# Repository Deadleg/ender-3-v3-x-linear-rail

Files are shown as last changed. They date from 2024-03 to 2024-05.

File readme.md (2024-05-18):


# Ender-3-v3-se-x-linear-rail
This mod replaces the X-axis v slot wheels with an MGN9 linear rail.

If you don't know if you need linear rails on the X-axis then you probably won't benefit from this. But if you
_want_ linear rails like I did, then enjoy.

- **Dimensional accuracy and flow calibration is required in order for the nut trap to fit the nuts securely**.
- [BOM](bom/bom.csv).
  - Either an MGN9C or MGN9H carriage can be used. Ideally use rails with some preload to improve wobble along the Y
  axis.
- Use [Voron print settings](https://docs.vorondesign.com/sourcing.html#print-settings).
  - Probably avoid PLA due to the nut trap only being two walls thick.
- No additional supports required.
- Print STLs in their default orientation.

After installation remember to re-calibrate the Z-offset and recreate the bed mesh.

Measurements and spacers inspired by https://www.printables.com/model/716958-linear-x-rail-mod-ender-3-v3-se. This
version doesn't sacrifice X-axis movement and doesn't need a new endstop. The nozzle sits a bit forward in the Y
axis.

See [results.md](results.md) for input shaper results.

Ender 3 V3 SE reference model taken from
https://www.printables.com/model/672045-ender-3-v3-se-reference-models-step-files.

# Development

Prerequisites:

- https://github.com/nophead/NopSCADlib/tree/master
- https://github.com/revarbat/BOSL

PYTHONPATH is required to generate the BOM with costs:

```bash
PYTHONPATH=$PWD ~/.local/share/OpenSCAD/libraries/NopSCADlib/scripts/make_all.py
```

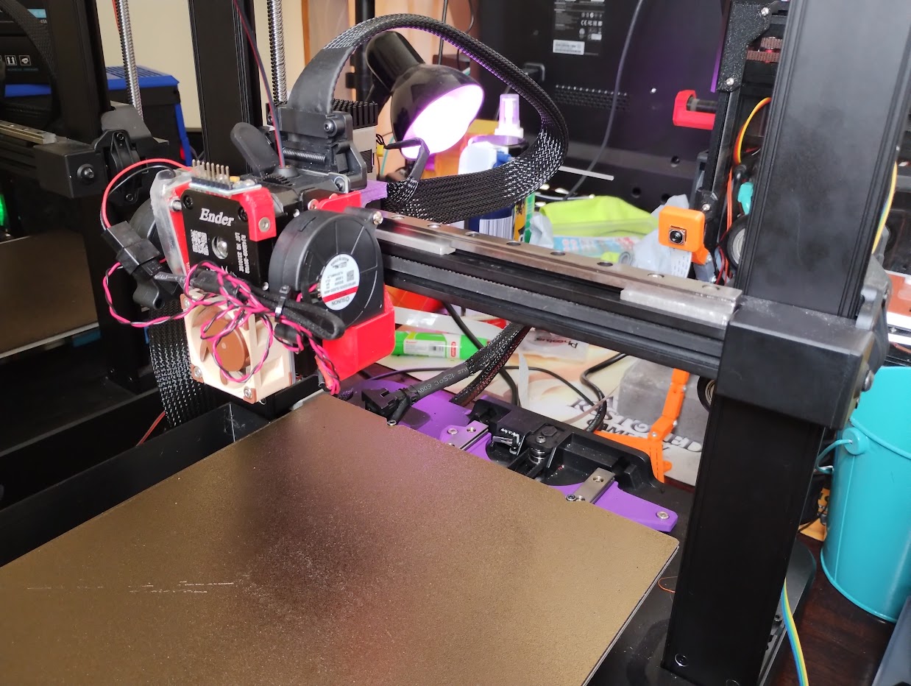
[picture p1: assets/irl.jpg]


<span></span>

---
## Table of Contents
1. [Parts list](#Parts_list)
1. [Carriage Assembly](#carriage_assembly)
1. [Linear Rail Assembly](#linear_rail_assembly)
1. [Carriage Rail Assembly](#carriage_rail_assembly)
1. [Toolhead Carriage Assembly](#toolhead_carriage_assembly)

<span></span>
[Top](#TOP)

---

## Parts list
| <span style="writing-mode: vertical-rl; text-orientation: mixed;">Carriage</span> | <span style="writing-mode: vertical-rl; text-orientation: mixed;">Linear&nbsp;Rail</span> | <span style="writing-mode: vertical-rl; text-orientation: mixed;">Carriage&nbsp;Rail</span> | <span style="writing-mode: vertical-rl; text-orientation: mixed;">Toolhead&nbsp;Carriage</span> | <span style="writing-mode: vertical-rl; text-orientation: mixed;">TOTALS</span> |  |
|---:|---:|---:|---:|---:|:---|
|  |  |  |  | | **Vitamins** |
| &nbsp;&nbsp;.&nbsp; | &nbsp;&nbsp;7&nbsp; | &nbsp;&nbsp;.&nbsp; | &nbsp;&nbsp;.&nbsp; |  &nbsp;&nbsp;7&nbsp; | &nbsp;&nbsp; Linear rail MGN9 x 300mm |
| &nbsp;&nbsp;.&nbsp; | &nbsp;&nbsp;1&nbsp; | &nbsp;&nbsp;.&nbsp; | &nbsp;&nbsp;.&nbsp; |  &nbsp;&nbsp;1&nbsp; | &nbsp;&nbsp; Linear rail carriage MGN9C |
| &nbsp;&nbsp;.&nbsp; | &nbsp;&nbsp;7&nbsp; | &nbsp;&nbsp;.&nbsp; | &nbsp;&nbsp;.&nbsp; |  &nbsp;&nbsp;7&nbsp; | &nbsp;&nbsp; Nut M3 hammer |
| &nbsp;&nbsp;2&nbsp; | &nbsp;&nbsp;.&nbsp; | &nbsp;&nbsp;.&nbsp; | &nbsp;&nbsp;.&nbsp; |  &nbsp;&nbsp;2&nbsp; | &nbsp;&nbsp; Nut M5 x 4mm  |
| &nbsp;&nbsp;.&nbsp; | &nbsp;&nbsp;.&nbsp; | &nbsp;&nbsp;4&nbsp; | &nbsp;&nbsp;.&nbsp; |  &nbsp;&nbsp;4&nbsp; | &nbsp;&nbsp; Screw M3 cap x  8mm |
| &nbsp;&nbsp;.&nbsp; | &nbsp;&nbsp;7&nbsp; | &nbsp;&nbsp;.&nbsp; | &nbsp;&nbsp;.&nbsp; |  &nbsp;&nbsp;7&nbsp; | &nbsp;&nbsp; Screw M3 cap x 10mm |
| &nbsp;&nbsp;.&nbsp; | &nbsp;&nbsp;.&nbsp; | &nbsp;&nbsp;.&nbsp; | &nbsp;&nbsp;2&nbsp; |  &nbsp;&nbsp;2&nbsp; | &nbsp;&nbsp; Screw M5 wafer head x  4mm |
| &nbsp;&nbsp;.&nbsp; | &nbsp;&nbsp;.&nbsp; | &nbsp;&nbsp;4&nbsp; | &nbsp;&nbsp;.&nbsp; |  &nbsp;&nbsp;4&nbsp; | &nbsp;&nbsp; Washer  M3 x 7mm x 0.5mm |
| &nbsp;&nbsp;2&nbsp; | &nbsp;&nbsp;22&nbsp; | &nbsp;&nbsp;8&nbsp; | &nbsp;&nbsp;2&nbsp; | &nbsp;&nbsp;34&nbsp; | &nbsp;&nbsp;Total vitamins count |
|  |  |  |  | | **3D printed parts** |
| &nbsp;&nbsp;.&nbsp; | &nbsp;&nbsp;1&nbsp; | &nbsp;&nbsp;.&nbsp; | &nbsp;&nbsp;.&nbsp; |  &nbsp;&nbsp;1&nbsp; | &nbsp;&nbsp;left_spacer.stl |
| &nbsp;&nbsp;.&nbsp; | &nbsp;&nbsp;1&nbsp; | &nbsp;&nbsp;.&nbsp; | &nbsp;&nbsp;.&nbsp; |  &nbsp;&nbsp;1&nbsp; | &nbsp;&nbsp;middle_spacer.stl |
| &nbsp;&nbsp;.&nbsp; | &nbsp;&nbsp;1&nbsp; | &nbsp;&nbsp;.&nbsp; | &nbsp;&nbsp;.&nbsp; |  &nbsp;&nbsp;1&nbsp; | &nbsp;&nbsp;right_spacer.stl |
| &nbsp;&nbsp;1&nbsp; | &nbsp;&nbsp;.&nbsp; | &nbsp;&nbsp;.&nbsp; | &nbsp;&nbsp;.&nbsp; |  &nbsp;&nbsp;1&nbsp; | &nbsp;&nbsp;toolhead_carriage_MGN9C.stl |
| &nbsp;&nbsp;1&nbsp; | &nbsp;&nbsp;.&nbsp; | &nbsp;&nbsp;.&nbsp; | &nbsp;&nbsp;.&nbsp; |  &nbsp;&nbsp;1&nbsp; | &nbsp;&nbsp;toolhead_carriage_MGN9H.stl |
| &nbsp;&nbsp;2&nbsp; | &nbsp;&nbsp;3&nbsp; | &nbsp;&nbsp;.&nbsp; | &nbsp;&nbsp;.&nbsp; | &nbsp;&nbsp;5&nbsp; | &nbsp;&nbsp;Total 3D printed parts count |

<span></span>
[Top](#TOP)

---

## Carriage Assembly
### Vitamins
|Qty|Description|
|---:|:---|
|2| Nut M5 x 4mm |

### 3D Printed parts

| 1 x toolhead_carriage_MGN9C.stl | 1 x toolhead_carriage_MGN9H.stl |
|---|---|
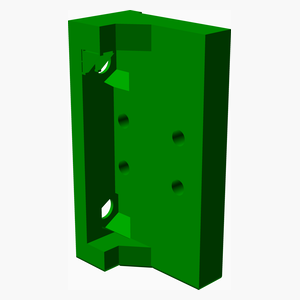
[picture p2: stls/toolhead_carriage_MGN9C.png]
toolhead_carriage_MGN9C.stl
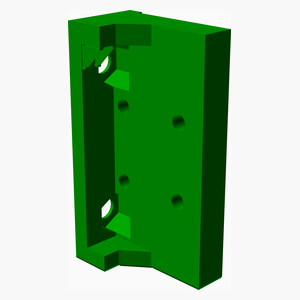
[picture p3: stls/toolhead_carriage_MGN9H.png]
toolhead_carriage_MGN9H.stl
|  |  

### Assembly instructions
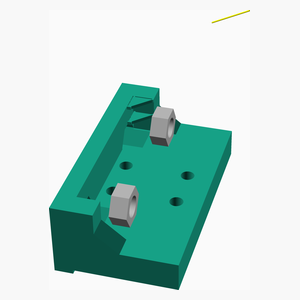
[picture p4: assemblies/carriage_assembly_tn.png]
carriage_assembly


First remove the two supports at the top of the model.

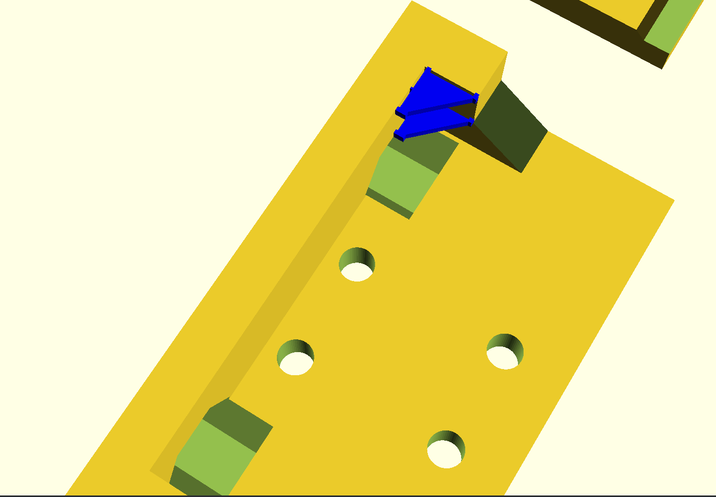
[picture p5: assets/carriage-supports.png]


The nuts should be a tight fit. If you have trouble pushing the nut in, check if there is any substantial corner
blobbing due to lack of pressure advance and/or insert an M5 screw from the otherside and tighten.

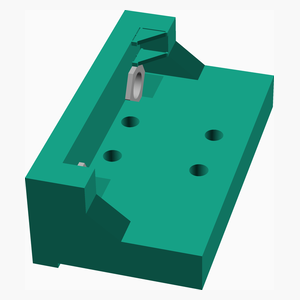
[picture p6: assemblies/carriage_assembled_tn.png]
carriage_assembled


<span></span>
[Top](#TOP)

---

## Linear Rail Assembly
### Vitamins
|Qty|Description|
|---:|:---|
|7| Linear rail MGN9 x 300mm|
|1| Linear rail carriage MGN9C|
|7| Nut M3 hammer|
|7| Screw M3 cap x 10mm|

### 3D Printed parts

| 1 x left_spacer.stl | 1 x middle_spacer.stl | 1 x right_spacer.stl |
|---|---|---|
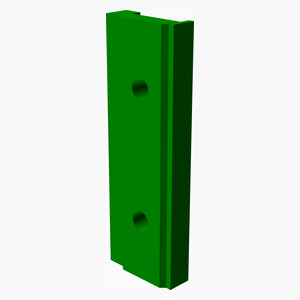
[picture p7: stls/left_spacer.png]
left_spacer.stl
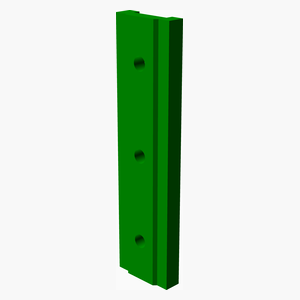
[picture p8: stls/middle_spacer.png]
middle_spacer.stl
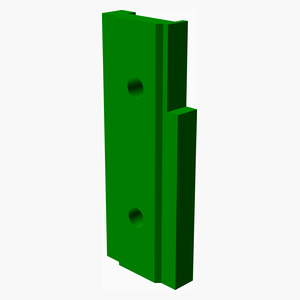
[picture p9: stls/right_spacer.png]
right_spacer.stl
|  |  |  

### Assembly instructions
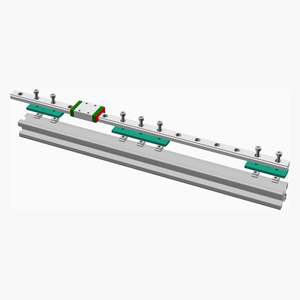
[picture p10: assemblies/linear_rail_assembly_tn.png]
linear_rail_assembly


Attach the spacers to the assembly, taking note that the left spacer is offset by one screw hole.

Remember to clean and lubricate both the carriage and rail.

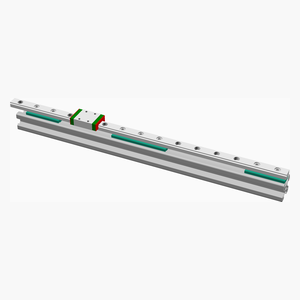
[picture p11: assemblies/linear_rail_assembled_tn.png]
linear_rail_assembled


<span></span>
[Top](#TOP)

---

## Carriage Rail Assembly
### Vitamins
|Qty|Description|
|---:|:---|
|4| Screw M3 cap x  8mm|
|4| Washer  M3 x 7mm x 0.5mm|

### Sub-assemblies

| 1 x carriage_assembly | 1 x linear_rail_assembly |
|---|---|
| carriage_assembled | linear_rail_assembled 

### Assembly instructions
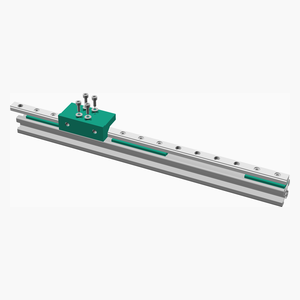
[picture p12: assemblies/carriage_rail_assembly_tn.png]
carriage_rail_assembly


Attach the carriage to the rail. Note that the front two screws won't be easily accessible once the PCB is mounted.

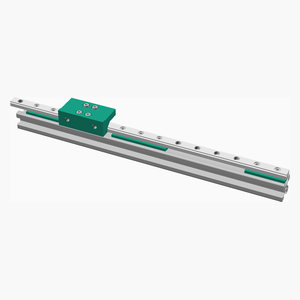
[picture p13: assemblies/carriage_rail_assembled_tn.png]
carriage_rail_assembled


<span></span>
[Top](#TOP)

---

## Toolhead Carriage Assembly
### Vitamins
|Qty|Description|
|---:|:---|
|2| Screw M5 wafer head x  4mm|

### Sub-assemblies

| 1 x carriage_rail_assembly |
|---|
| carriage_rail_assembled 

### Assembly instructions
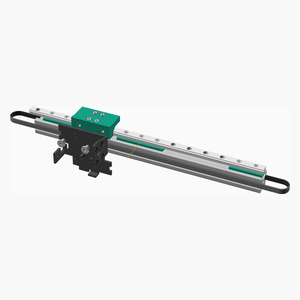
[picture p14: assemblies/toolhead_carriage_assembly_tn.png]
toolhead_carriage_assembly


Screw the frame into the carriage, ensuring that the frame is flush on the carriage. Remember to insert the belts
before re-assembling the everything else.

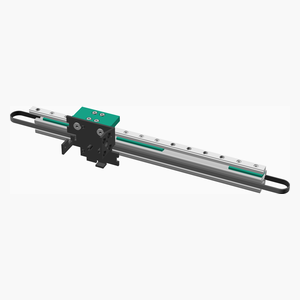
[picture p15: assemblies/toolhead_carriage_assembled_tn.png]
toolhead_carriage_assembled


<span></span>
[Top](#TOP)

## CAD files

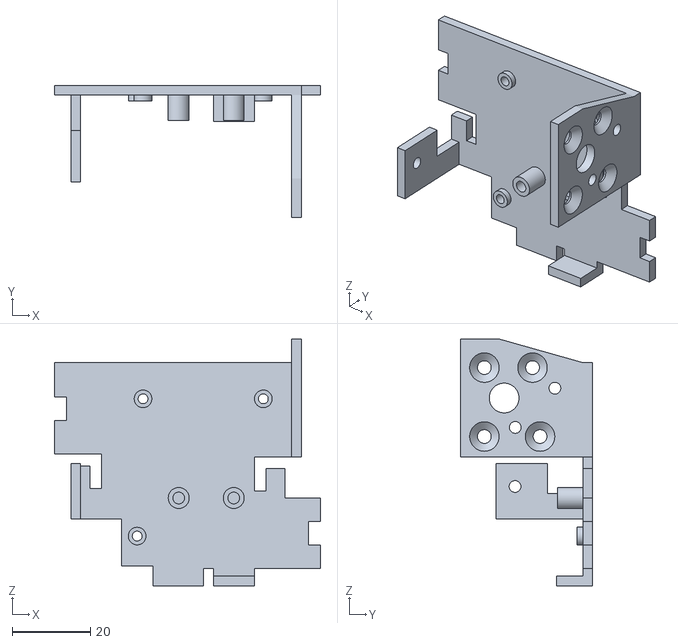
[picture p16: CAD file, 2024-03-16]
ender-3-v3-se-reference-models-step-files/frame.stl
67.8 x 33.7 x 62.9

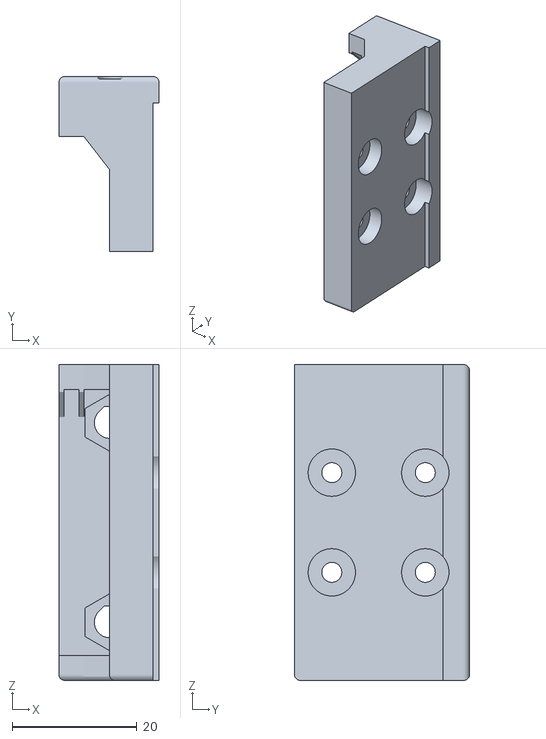
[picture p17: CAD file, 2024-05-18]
stls/toolhead_carriage_MGN9H.stl
16.1 x 28.1 x 50.7

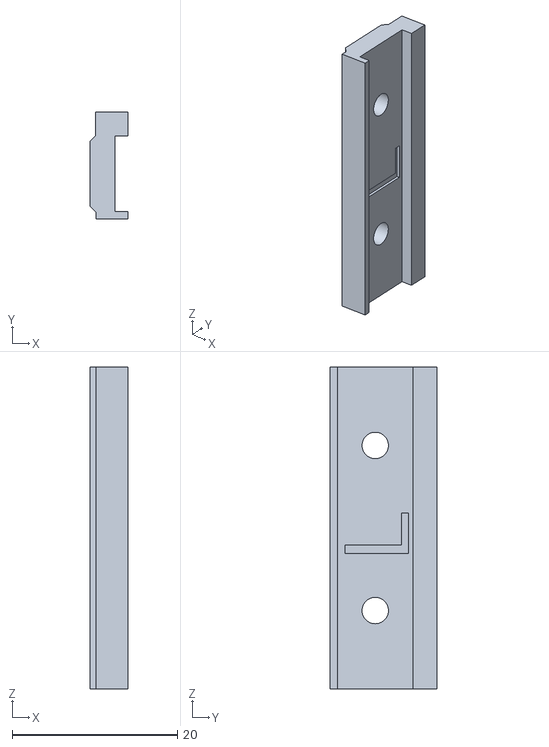
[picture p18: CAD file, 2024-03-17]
stls/left_spacer.stl
4.60 x 13.0 x 39.0

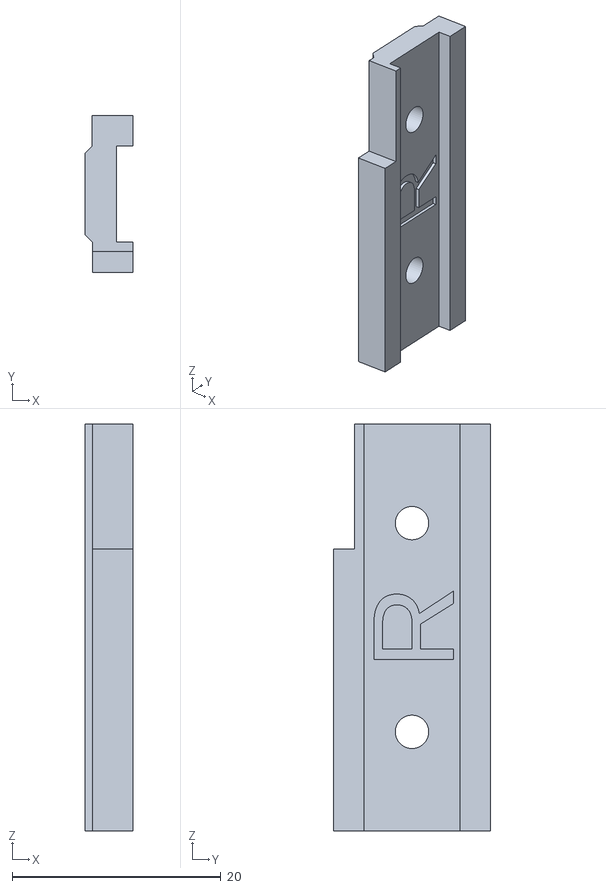
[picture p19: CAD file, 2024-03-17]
stls/right_spacer.stl
4.60 x 15.0 x 39.0

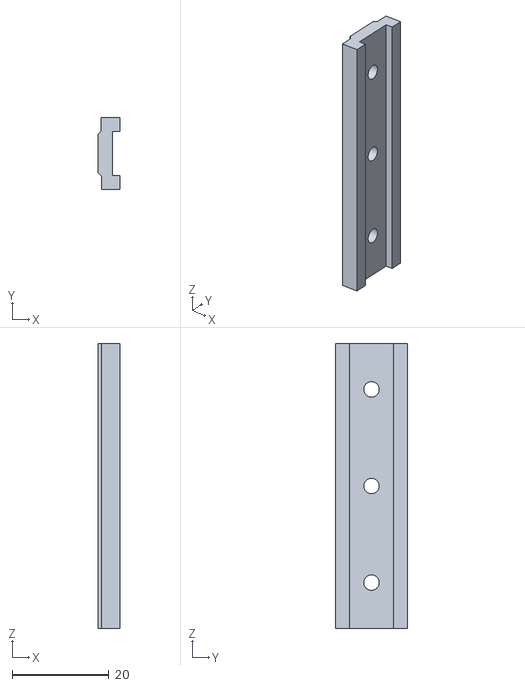
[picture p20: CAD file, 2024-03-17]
stls/middle_spacer.stl
4.60 x 15.0 x 59.0

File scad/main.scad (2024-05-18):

//! This mod replaces the X-axis v slot wheels with an MGN9 linear rail.
//!
//! If you don't know if you need linear rails on the X-axis then you probably won't benefit from this. But if you
//! _want_ linear rails like I did, then enjoy.
//!
//! - **Dimensional accuracy and flow calibration is required in order for the nut trap to fit the nuts securely**.
//! - [BOM](bom/bom.csv).
//!   - Either an MGN9C or MGN9H carriage can be used. Ideally use rails with some preload to improve wobble along the Y
//!   axis.
//! - Use [Voron print settings](https://docs.vorondesign.com/sourcing.html#print-settings).
//!   - Probably avoid PLA due to the nut trap only being two walls thick.
//! - No additional supports required.
//! - Print STLs in their default orientation.
//!
//! After installation remember to re-calibrate the Z-offset and recreate the bed mesh.
//!
//! Measurements and spacers inspired by https://www.printables.com/model/716958-linear-x-rail-mod-ender-3-v3-se. This
//! version doesn't sacrifice X-axis movement and doesn't need a new endstop. The nozzle sits a bit forward in the Y
//! axis.
//!
//! See [results.md](results.md) for input shaper results.
//!
//! Ender 3 V3 SE reference model taken from
//! https://www.printables.com/model/672045-ender-3-v3-se-reference-models-step-files.
//!
//! # Development
//!
//! Prerequisites:
//!
//! - https://github.com/nophead/NopSCADlib/tree/master
//! - https://github.com/revarbat/BOSL
//!
//! PYTHONPATH is required to generate the BOM with costs:
//!
//! ```bash
//! PYTHONPATH=$PWD ~/.local/share/OpenSCAD/libraries/NopSCADlib/scripts/make_all.py
//! ```
//!
//! ![assets/irl.jpg](assets/irl.jpg)
include <BOSL/shapes.scad>;
include <NopSCADlib/lib.scad>;
include <v-slot-customizer-and-openscad-library/v-slot_lib.scad>;

show_rail = true;

show_toolhead = true;

mount_thickness = 7;
mount_extra_width = 1;

bracket_mount_screw_x = 32;

metal_braket_space = 4;

bracket_extra_width = 21;

carriage_type = "MGN9C"; // [MGN9H, MGN9C]

mount_type = "Hex nut"; // [Hex nut, Square nut, Threaded insert]

// Select the component to export to STL.
print_component = "None"; //[Carriage, Spacers]

tolerance = 0.1;

mounting_carriage = carriage_type == "MGN9C" ? MGN9C_carriage : MGN9H_carriage;

rail_offset = 2.8 - 0.4; // The mounting blocks of the original model.

print_orientation = print_component != "None";

_show_rail = print_component != "None" ? false : show_rail;

rail_pos = 60;

$fn = 60;

M5x4 = [ "M5x4", 4, 10, 8.5, 5, 7.5, 0.5, 7.5, 7.5, 3.5, 0.8 ];
block_width = 15;
middle_block_width = rail_pitch(MGN9) * 3 - 1;

block_depth = 0.6;

end_block_width = rail_pitch(MGN9) * 2 - 1;

module toolhead()
{
    not_on_bom()
    {
        if (_show_rail && show_toolhead)
        {
            // Offset is eyeballed.
            color([ 0.3, 0.3, 0.3 ]) translate([ -2.45 + rail_pos, 16, 19 + 3.5 - rail_offset ]) rotate([ 0, 0, 180 ])
                import("../ender-3-v3-se-reference-models-step-files/full-toolhead.stl");
        }
    }
}

module toolhead_frame()
{
    not_on_bom()
    {
        if (_show_rail)
        {
            if (show_toolhead)
            {
                color([ 0.3, 0.3, 0.3 ]) translate([ 28 + rail_pos, 14.8, 19.1 + 3.5 - rail_offset ])
                    rotate([ 0, 0, 180 ]) import("../ender-3-v3-se-reference-models-step-files/frame.stl");
            }
        }
    }
}

//! Attach the spacers to the assembly, taking note that the left spacer is offset by one screw hole.
//!
//! Remember to clean and lubricate both the carriage and rail.
module linear_rail_assembly()
{
    pose(a = [ 55, 0, 205 ]) assembly("linear_rail")
    {
        if (_show_rail)
        {
            explode(10) rail_assembly(mounting_carriage, 300, rail_pos, carriage_end_colour = "green",
                                      carriage_wiper_colour = "red");
        }
        rotation = print_component == "Spacers" ? 180 : 0;
        distance = print_component == "Spacers" ? rail_pitch(MGN9) * 3 : rail_pitch(MGN9) * 7 - rail_pitch(MGN9) / 2;
        rotate([ rotation, 0, 0 ])
        {
            middle_spacer_assembly();
            translate([ -distance, 0, 0 ]) right_spacer_assembly();
            translate([ distance - rail_pitch(MGN9), 0, 0 ]) left_spacer_assembly();
        }
        explode(-10) not_on_bom()
        {
            if (_show_rail)
            {
                color("silver") translate([ -150, 0, -extrusion_height(E2020) / 2 - rail_offset ]) rotate([ 0, 90, 0 ])
                    V_slot("20x20", 290);
            }
        }
    }
}

//! Attach the carriage to the rail. Note that the front two screws won't be easily accessible once the PCB is mounted.
module carriage_rail_assembly()
{
    pose(a = [ 55, 0, 205 ]) assembly("carriage_rail")
    {
        linear_rail_assembly();
        carriage_assembly();
        carriage_screws();
    }
}

//! Screw the frame into the carriage, ensuring that the frame is flush on the carriage. Remember to insert the belts
//! before re-assembling the everything else.
module toolhead_carriage_assembly()
{
    pose(a = [ 55, 0, 205 ]) assembly("toolhead_carriage")
    {
        carriage_rail_assembly();
        explode([ 0, 20, 0 ]) toolhead_frame();
        explode([ 0, 40, 0 ]) frame_screws();

        translate([ 0, 0, -extrusion_height(E2020) / 2 - rail_offset ])
        {
            if (_show_rail)
            {
                not_on_bom()
                {
                    belt(GT2x6, [
                        [ 170, 0, -extrusion_height(E2020) / 2 + 1 ], [ -170, 0, -extrusion_height(E2020) / 2 + 1 ]
                    ]);
                }
            }
        }
    }
}

module middle_spacer_stl()
{
    stl("middle_spacer")
    {
        rotate([ 0, 90, 0 ]) difference()
        {
            translate([ -middle_block_width / 2, -block_width / 2, -rail_offset - block_depth ])
                cube([ middle_block_width, block_width, rail_offset + block_depth + 1.6 ]);
            translate([ -150, 0, -extrusion_height(E2020) / 2 - rail_offset + tolerance ]) rotate([ 0, 90, 0 ])
                V_slot("20x20", 300);
            translate([ 0, -tolerance, 0 ]) hull() rail(MGN9, 300);
            translate([ 0, tolerance, 0 ]) hull() rail(MGN9, 300);

            translate([ 0, 0, -rail_offset * 2 ])
                rail_hole_positions(MGN9, middle_block_width, first = 0, screws = 3, both_ends = true)
            {
                cylinder(h = 20, r = screw_radius(M3_cap_screw) + tolerance);
            }
        }
    }
}

// Trim for the left side where the x motor mount overlaps with the extrusion.
module two_hole_spacer(is_left)
{

    difference()
    {
        // 1 mm between the rail and x-motor
        trimmed_width = block_width / 2 - (block_width - rail_width(MGN9) - 2) / 2;
        trim_distance = block_width / 2 - trimmed_width;
        union()
        {

            translate([ -end_block_width / 2, -block_width / 2 + trim_distance, -rail_offset - block_depth ])
                cube([ end_block_width, block_width - trim_distance, rail_offset + block_depth + 1.6 ]);
            if (is_left == false)
            {
                translate([ 12 - end_block_width / 2, -block_width / 2, -rail_offset - block_depth ])
                    cube([ end_block_width - 12, block_width, rail_offset + block_depth + 1.6 ]);
            }
        }
        // translate([ 0, 0, -extrusion_height(E2020) / 2 - rail_offset ]) rotate([ 0, 90, 0 ]) extrusion(E2020, 300);
        translate([ -150, 0, -extrusion_height(E2020) / 2 - rail_offset + tolerance ]) rotate([ 0, 90, 0 ])
            V_slot("20x20", 300);

        translate([ 0, -tolerance, 0 ]) hull() rail(MGN9, 300);
        translate([ 0, tolerance, 0 ]) hull() rail(MGN9, 300);

        translate([ 0, 0, -rail_offset * 2 ])
            rail_hole_positions(MGN9, end_block_width, first = 0, screws = 2, both_ends = true)
        {
            cylinder(h = 20, r = screw_radius(M3_cap_screw) + tolerance);
        }

        label = is_left ? "L" : "R";
        rotate([ 0, 0, 180 ]) translate([ -4, -4, -0.4 ]) linear_extrude(1) text(label, size = 8);
    }
}

module middle_spacer_screws()
{
    if (show_rail)
    {
        rail_screws(MGN9, middle_block_width, 6, screws = 3, index_screws = 0);
        rail_hole_positions(MGN9, middle_block_width, screws = 3)
        {
            translate([ 0, 0, -rail_offset - carriage_clearance(E2020) + t_nut_tab(M3_hammer_nut)[1] - 0.1 ])
                rotate([ 180, 0, 0 ]) sliding_t_nut(M3_hammer_nut);
        }
    }
}

module end_spacer_screws()
{
    if (show_rail)
    {
        rail_screws(MGN9, end_block_width, 6, screws = 2, index_screws = 0);
        rail_hole_positions(MGN9, end_block_width, screws = 2)
            translate([ 0, 0, -rail_offset - carriage_clearance(E2020) + t_nut_tab(M3_hammer_nut)[1] - 0.1 ])
                rotate([ 180, 0, 0 ]) sliding_t_nut(M3_hammer_nut);
    }
}
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

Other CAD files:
stls/toolhead_carriage_MGN9C.stl

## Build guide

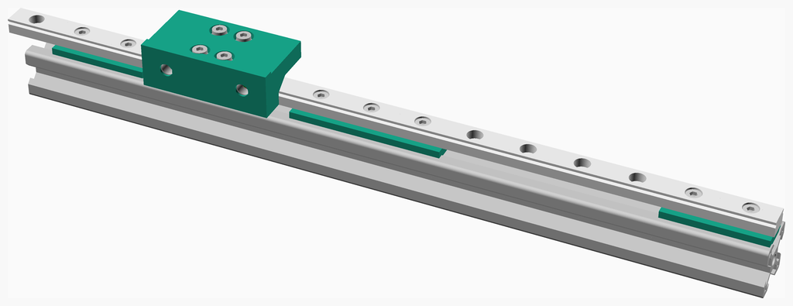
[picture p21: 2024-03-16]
assemblies/carriage_rail_assembled.png

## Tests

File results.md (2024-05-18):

# Results

My two SEs are almost identical with the following mods:

- Linear y rails
- Dual 5015 fans
- Low profile 40mm fan mount

The linear Y rails are cheap ones from Aliexpress with enough preload to prevent them from sliding by themselves. 

The linear X rails used are MGN9C and have next to no preload with so the carriage able to slide down the rail without any other force except for gravity. There is a bit of Y axis movement from the toolhead due to the rail carriage moving and not (as far as I can tell) the printed parts.

# V1

|Axis|Printer 1|Printer 2|
|---|---|---|
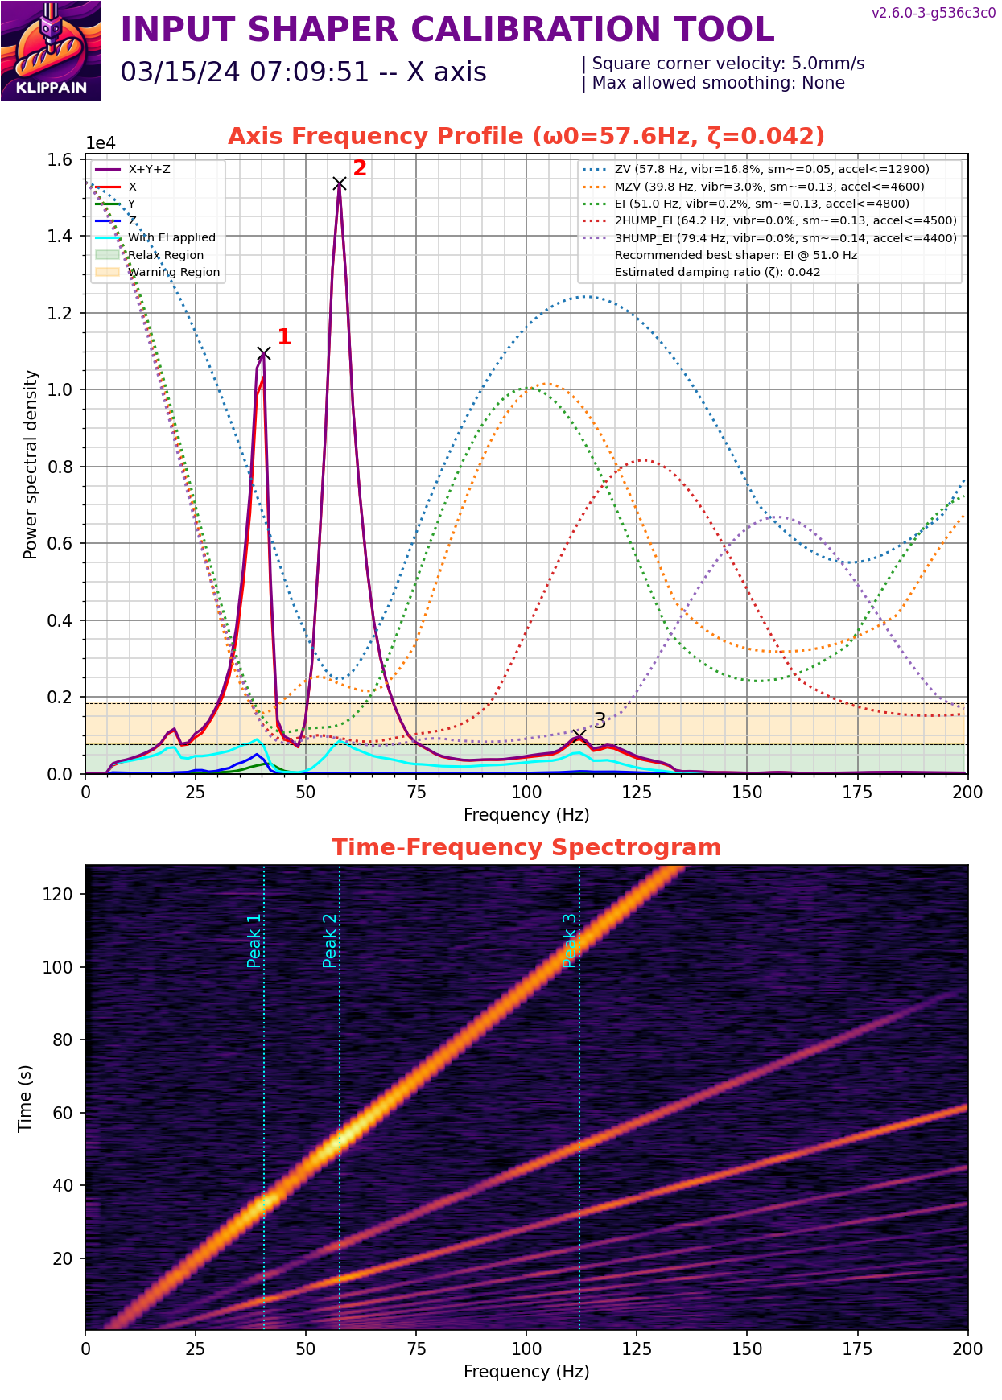
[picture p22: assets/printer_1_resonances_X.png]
printer_1_x
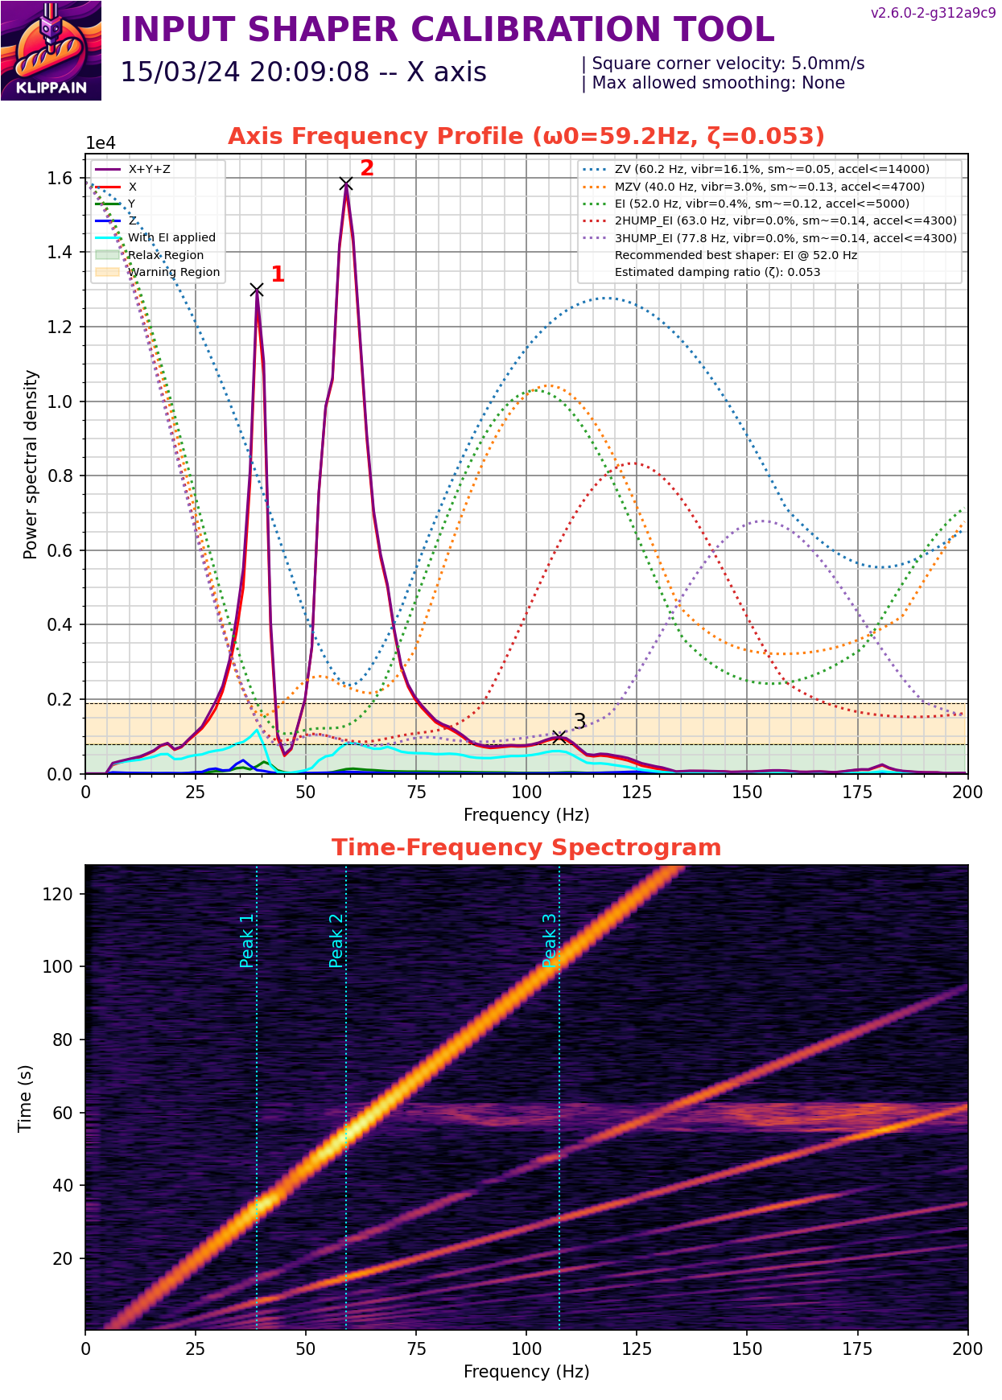
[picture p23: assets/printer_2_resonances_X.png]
printer_2_x
|X||
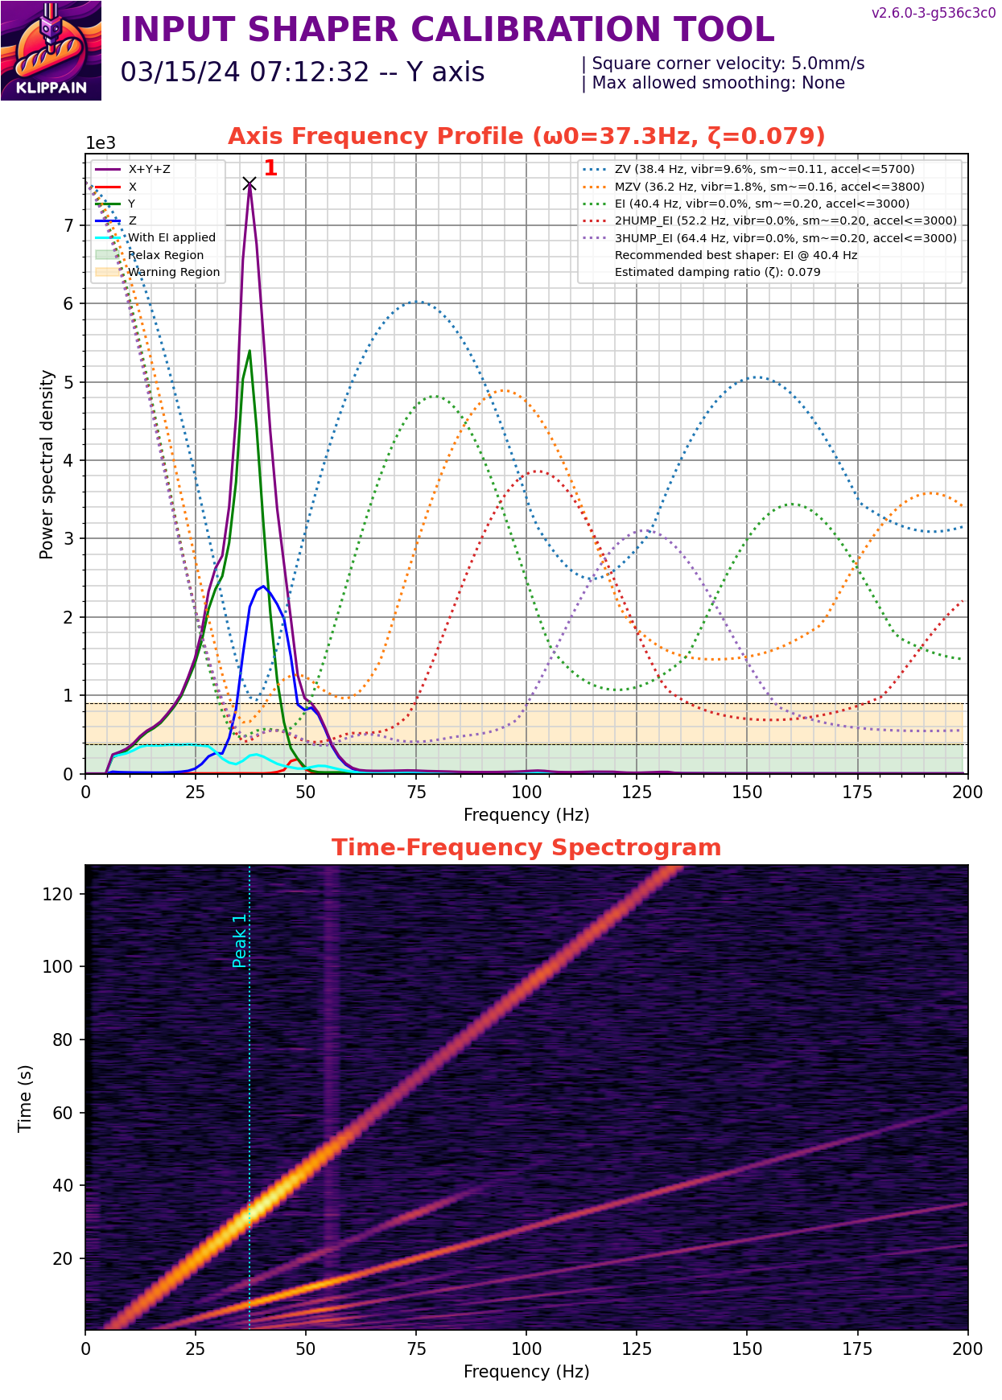
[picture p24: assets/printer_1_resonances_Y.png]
printer_1_y
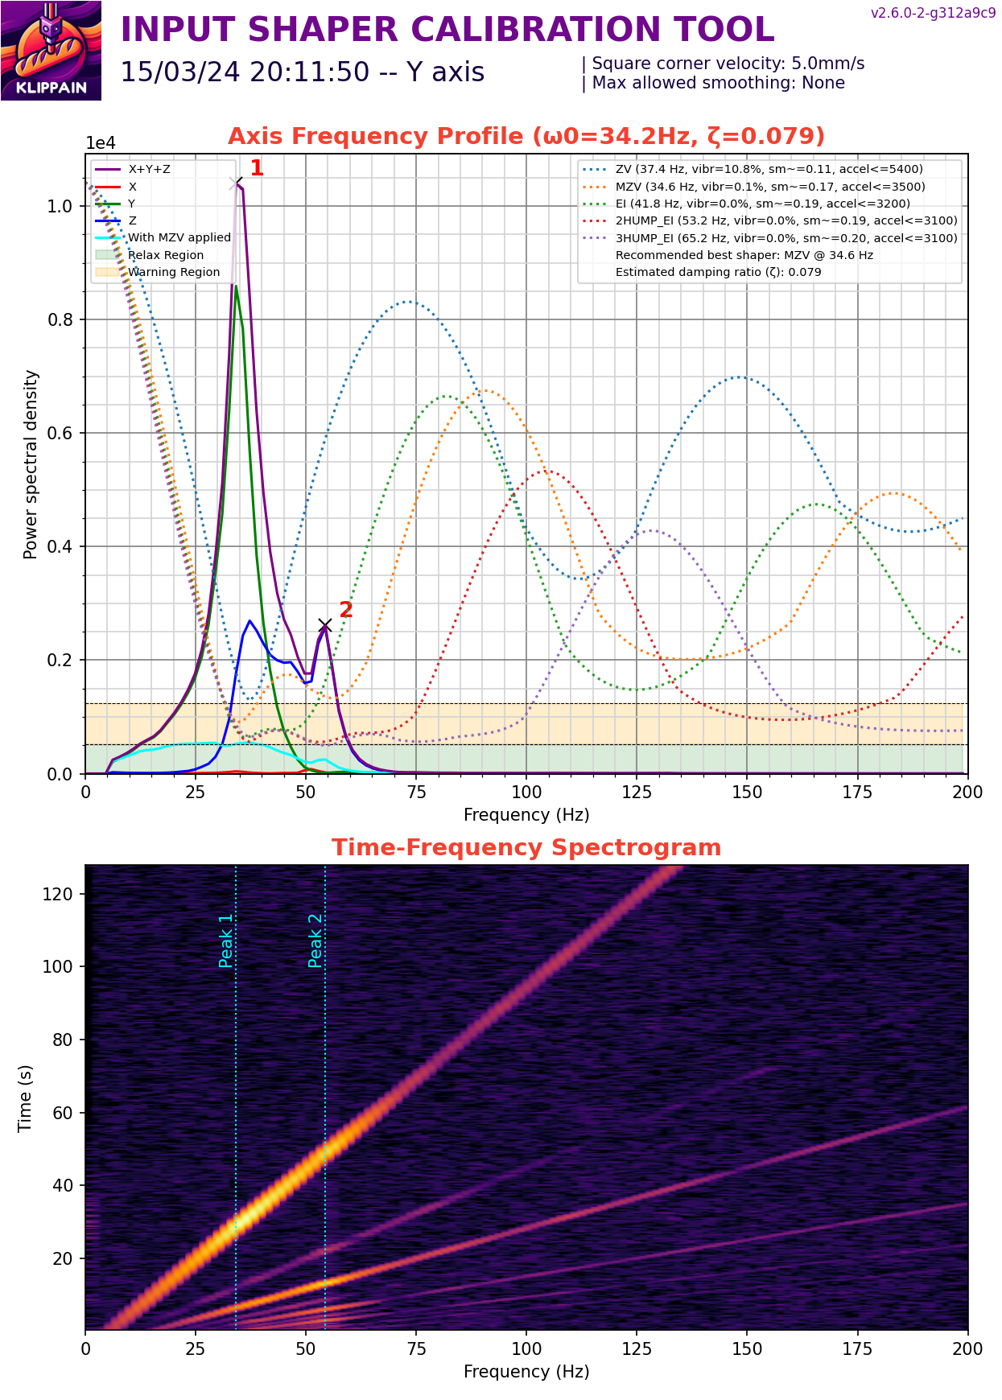
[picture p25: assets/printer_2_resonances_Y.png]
printer_2_y
|Y|||

# V2

V2 lowers the rail a little bit and adds a groove into the spacers to allow the rail to settle in the groove a little better.

There seems to be less vibrations on the X axis though I can't say that the belt tension is the same. The double peak resonances remain. The toolhead wobbles a less under my touch, but I can definitly feel the carriage having some play.

I purchased some MGN9H rails which have little to no preload and moves down the rail without any external forces. I tried my luck with a second set of rails, one of which has enough preload to prevent the carriage from sliding on its own.

I did the following experiments in this order:

- Using the V1 Backplate from https://www.printables.com/model/716958-linear-x-rail-mod-ender-3-v3-se. Used V1 because I already had that printed.
- Using V2 on MGN9C, replaced the Y motor with a same model, changed the Y pully to 30T, and trammed the linear Y rails more carefully.
- Using V2 on a no-preloaded MGN9H.
- Using V2 on a preloaded MGN9H.

I did not control for belt tension and other variables, so these graphs should reflect the general trends/order of magnitude estimates of vibrations and not a 1-to-1 comparison.

|Axis|Ben's V1|V2 MGN9C|V2 MGN9H no preload|V2 MGN9H preloaded|
|---|---|---|---|---|
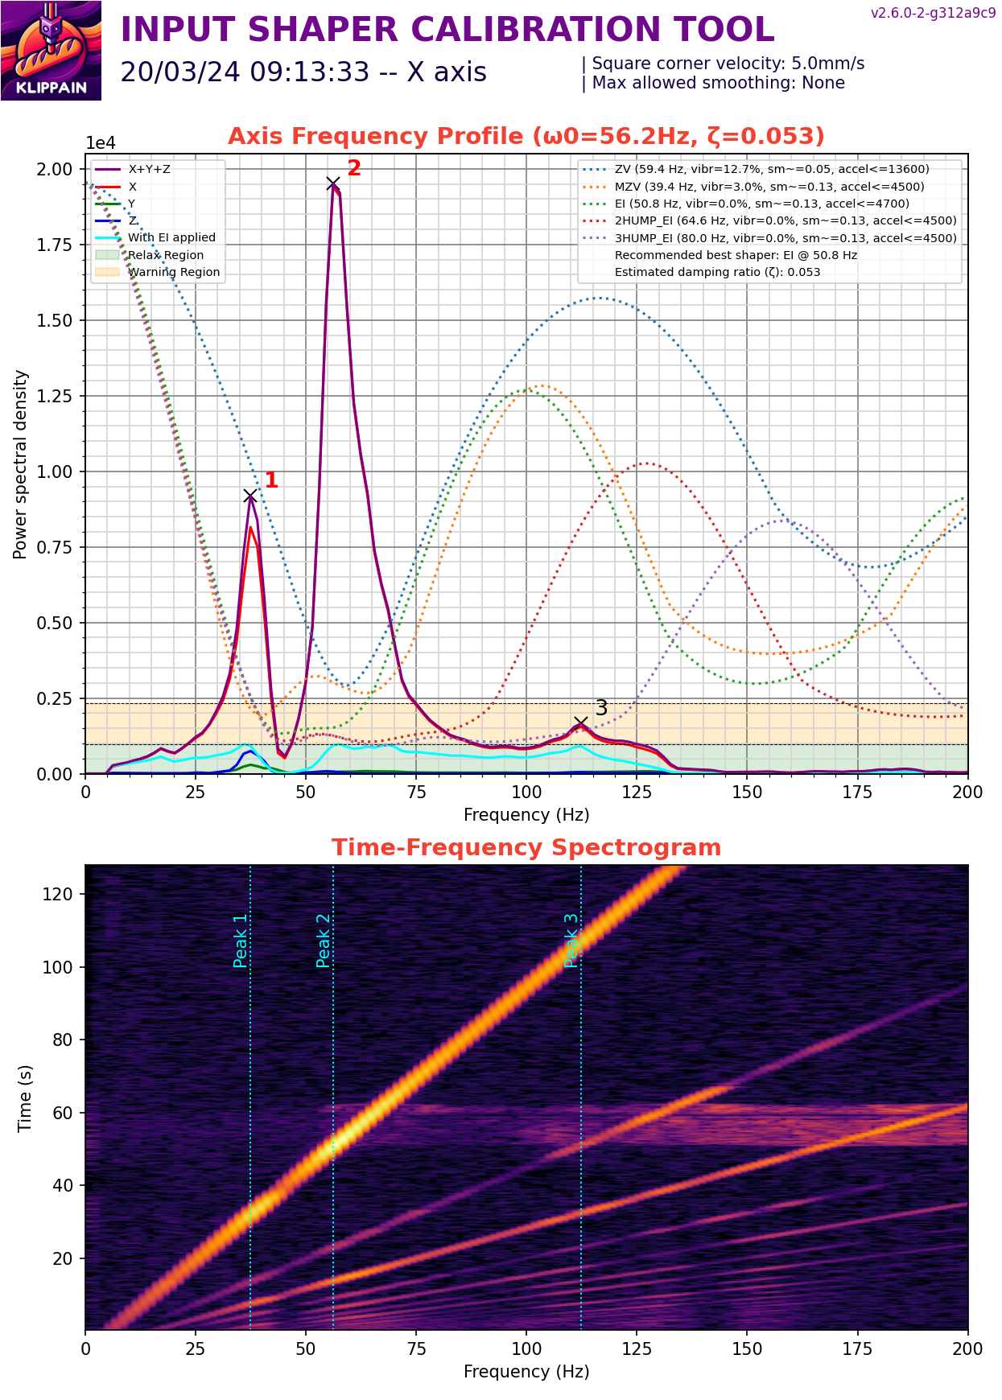
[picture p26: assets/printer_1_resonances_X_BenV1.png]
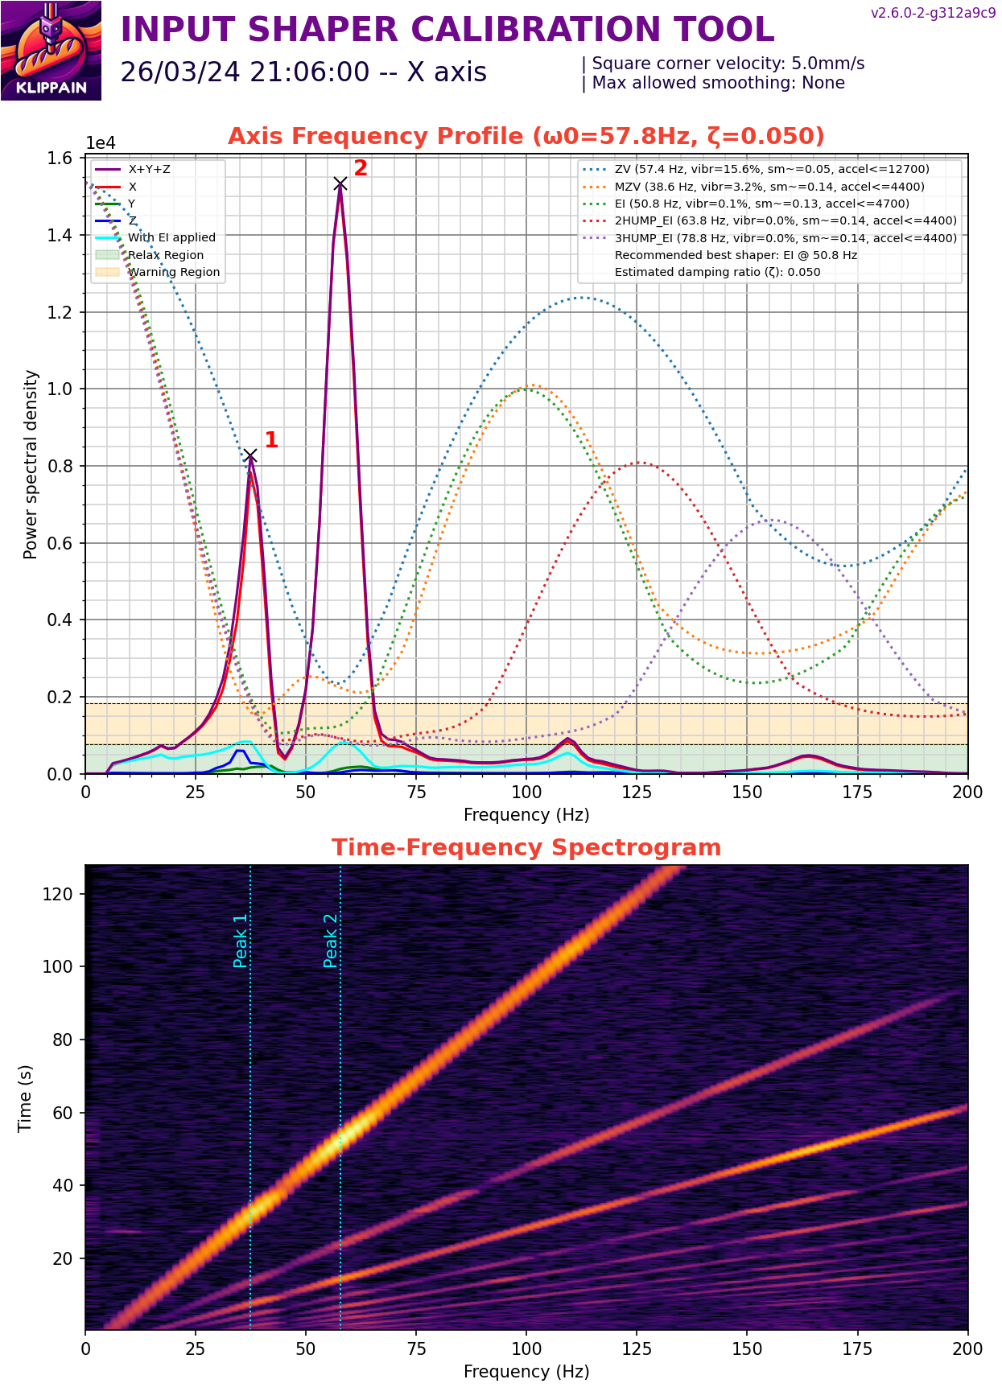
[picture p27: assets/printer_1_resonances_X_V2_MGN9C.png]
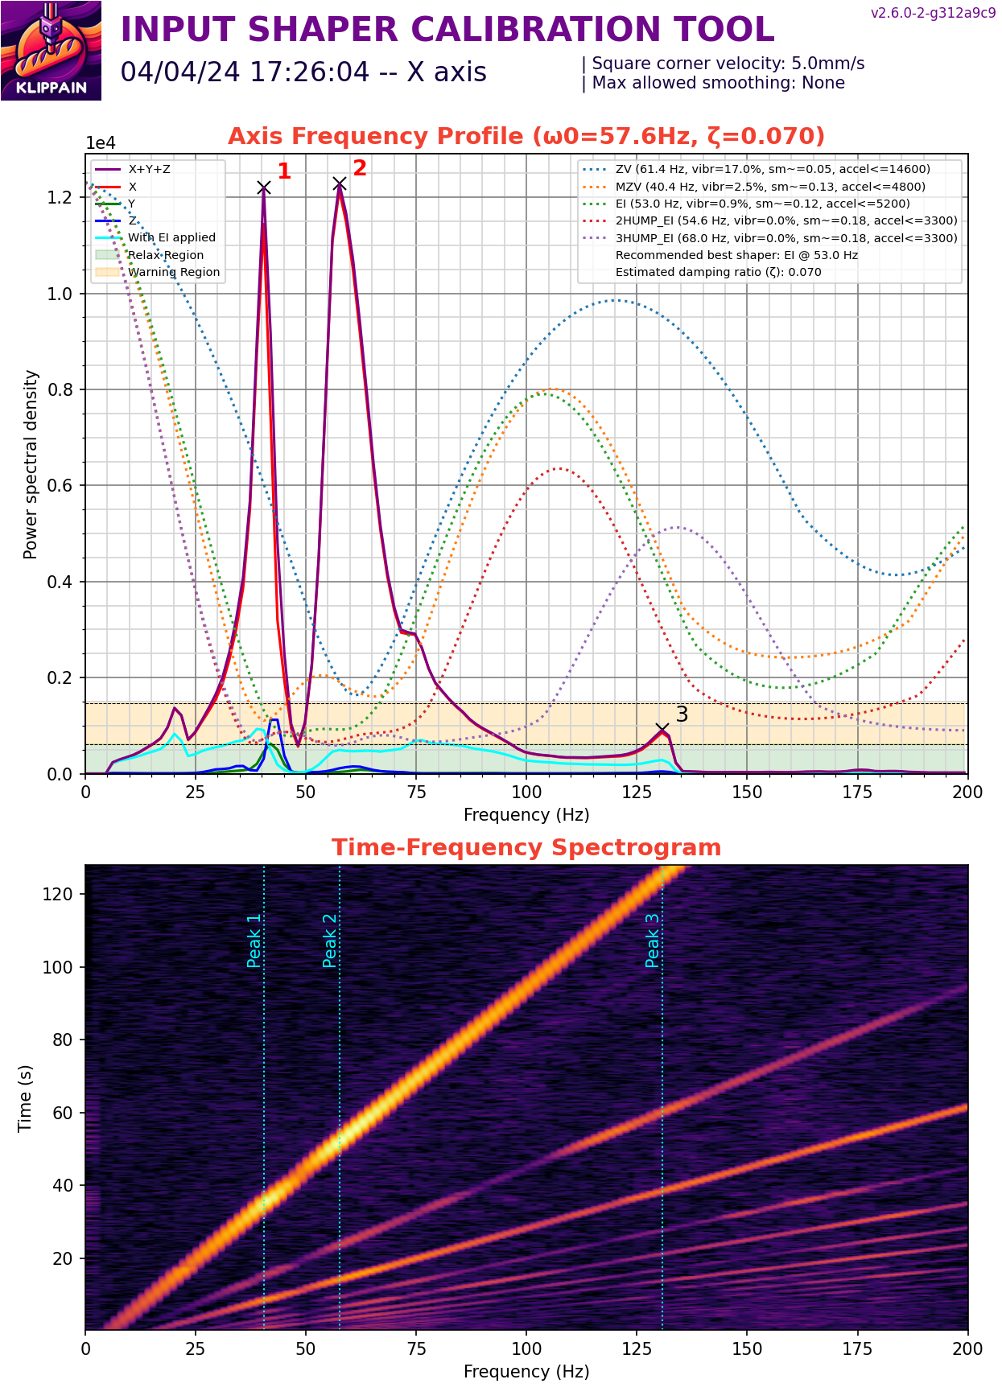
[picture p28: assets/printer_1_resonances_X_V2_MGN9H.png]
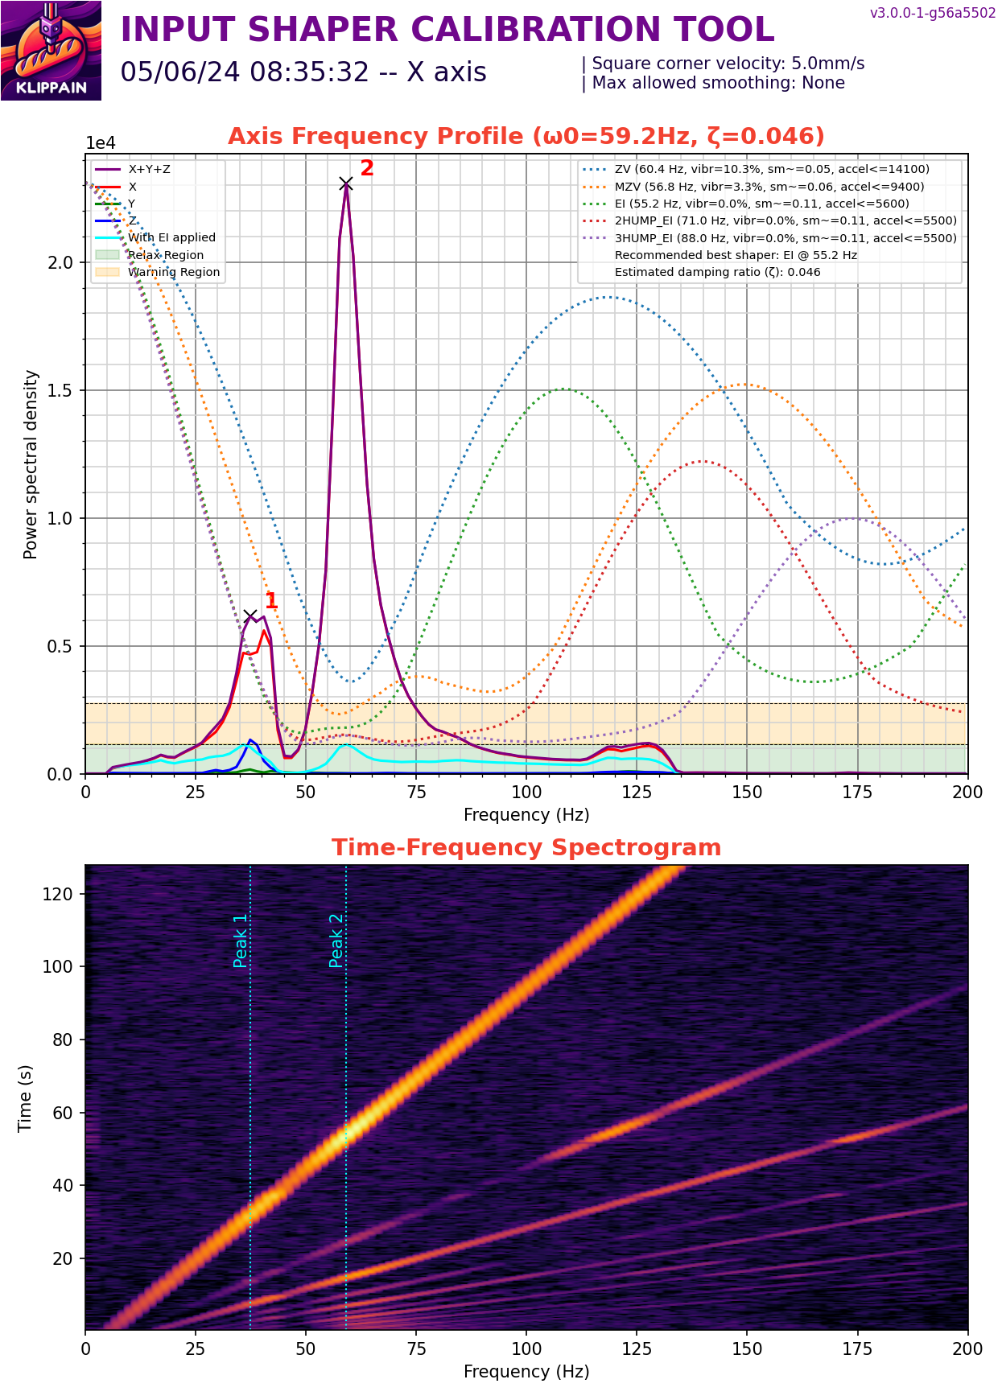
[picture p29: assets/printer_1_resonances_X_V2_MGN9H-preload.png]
X||||
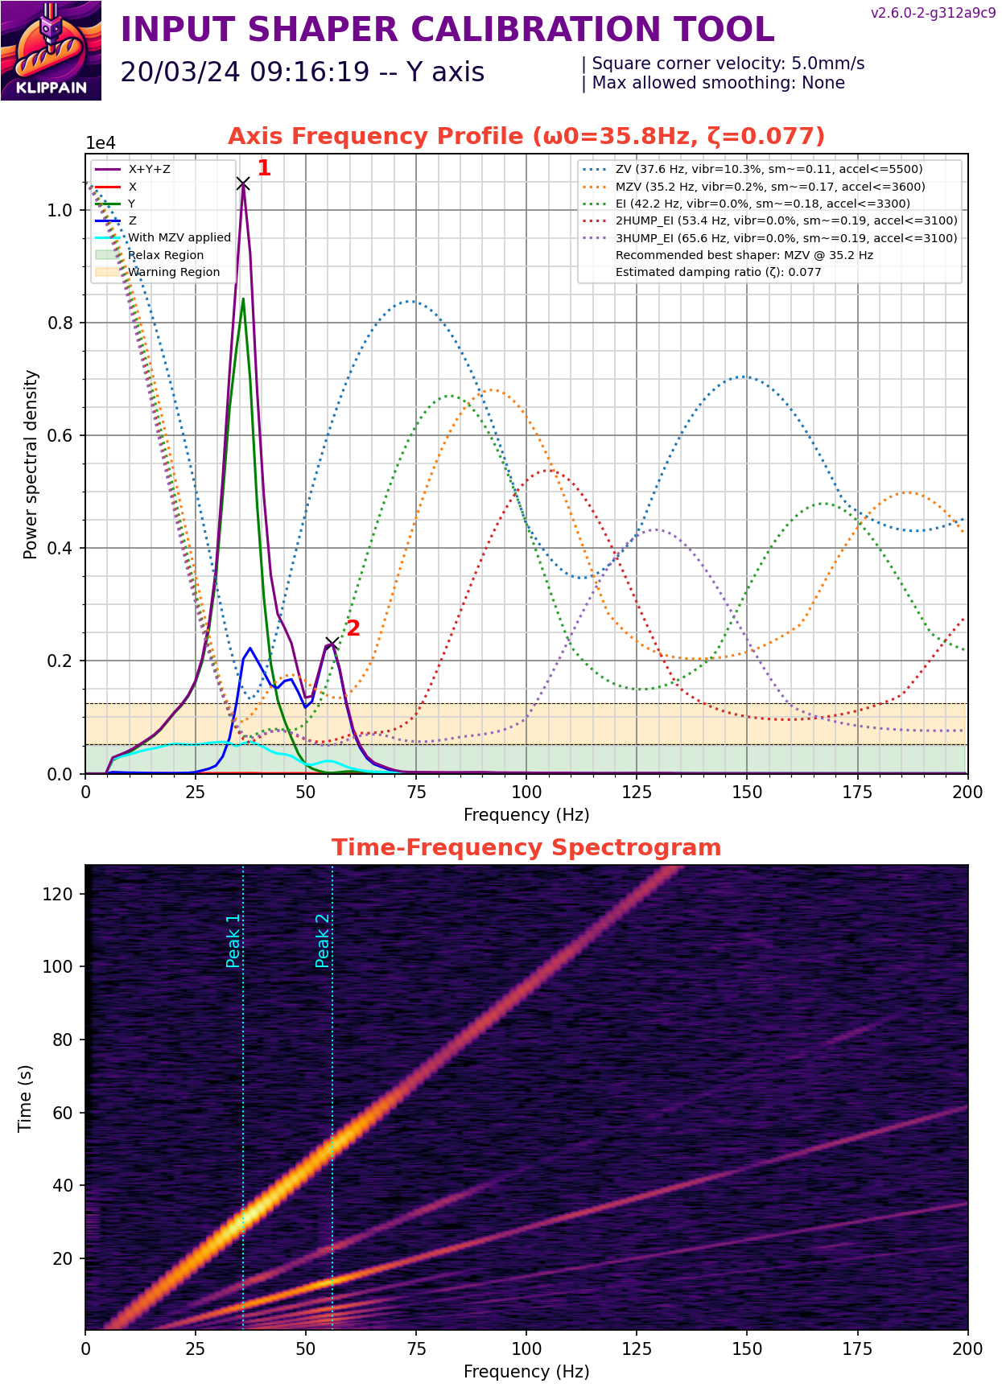
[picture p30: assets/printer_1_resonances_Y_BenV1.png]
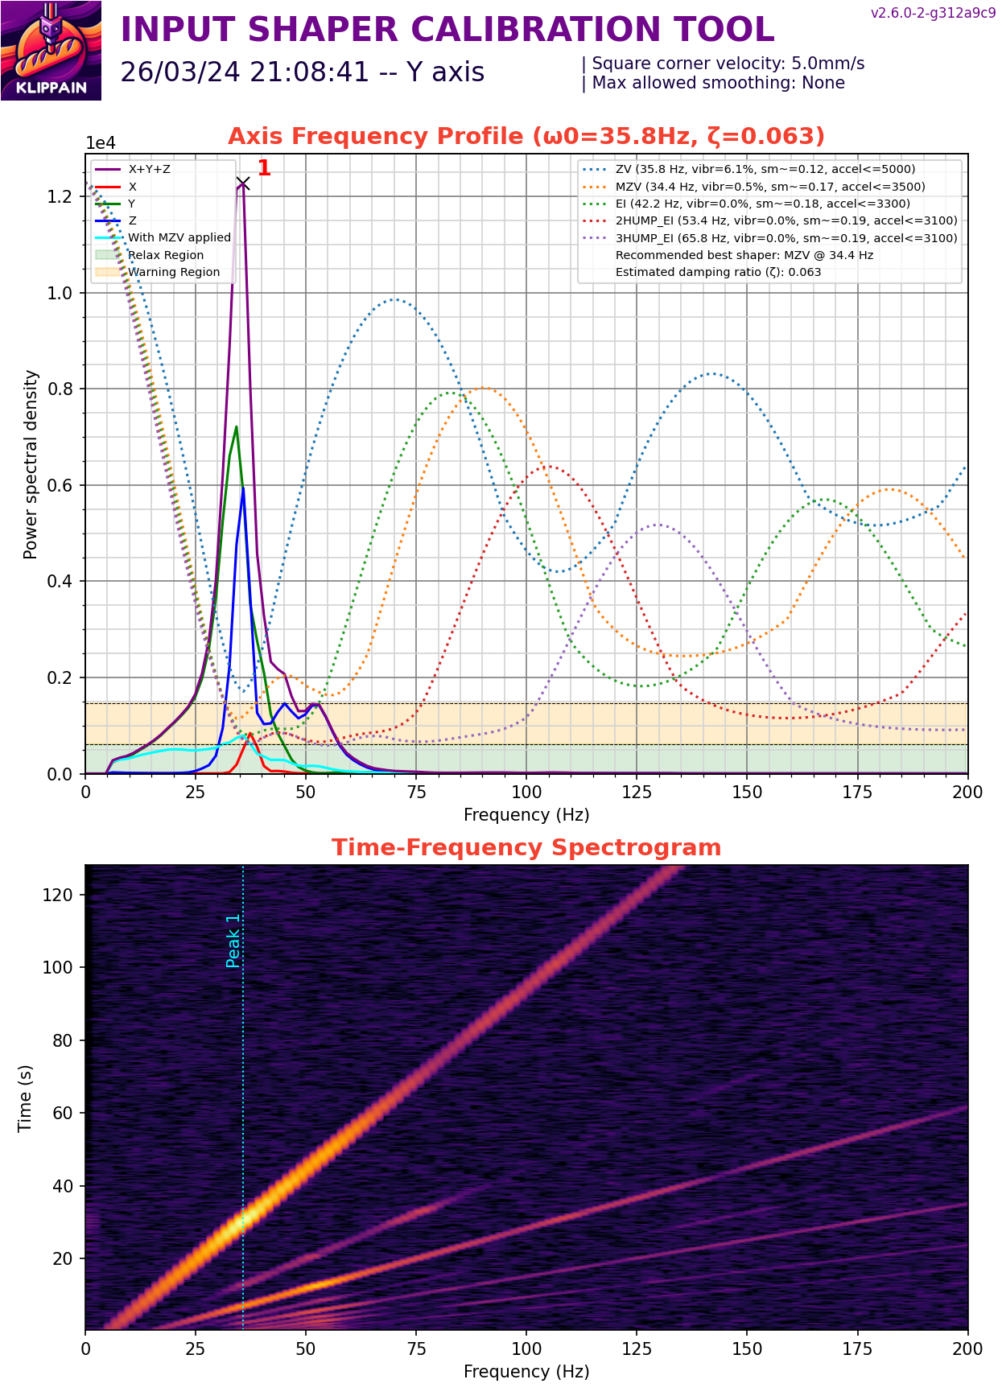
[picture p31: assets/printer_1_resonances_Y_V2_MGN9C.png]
Y||||

On the X axis all of the graphs are on the same order of magnitude, with the results improving with the MGN9H and improving again with the preloaded rail. With a max accel of ~5600 mm/s^2 this matches similar results I had using the V-slot wheels.

Tramming the Y rails has improved the second peak, though the vibrations on the last result is significantly higher.

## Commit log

2024-03-16 feat: initial commit
    [bom.csv, frame.stl, left_spacer.stl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]
2024-03-17 feat: lower rail into spacers with cutout
    [bom.csv, left_spacer.stl, main.scad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]
2024-05-18 feat: add chamfers and screw holes
    I noticed that the PCB screws stuck out of the aluminium bracket and
    potentially put too puch stress on the nut trap.
    [bom.csv, main.scad, toolhead_carriage_MGN9C.stl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]
